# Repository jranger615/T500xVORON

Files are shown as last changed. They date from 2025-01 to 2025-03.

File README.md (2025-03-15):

### If inclined to send a tip for my hard work:
* Paypal: Jeff.b.ranger@gmail.com
* Venmo: @Jeff-Ranger-1

<h2>This is a modificed Voron build using Trist0ne initial configurations but with less complexity. This uses the T500 stock breakout board and will mostly rely on Configuration Changes and Soldering wires/Changing ends for your stealthburner to fit.</h2>

*** 3/5/25 - Update - Changed Printer.cfg, Filament.cfg, and added Runout.cfg. Runout.cfg is commented out in the includes in printer.cfg by default

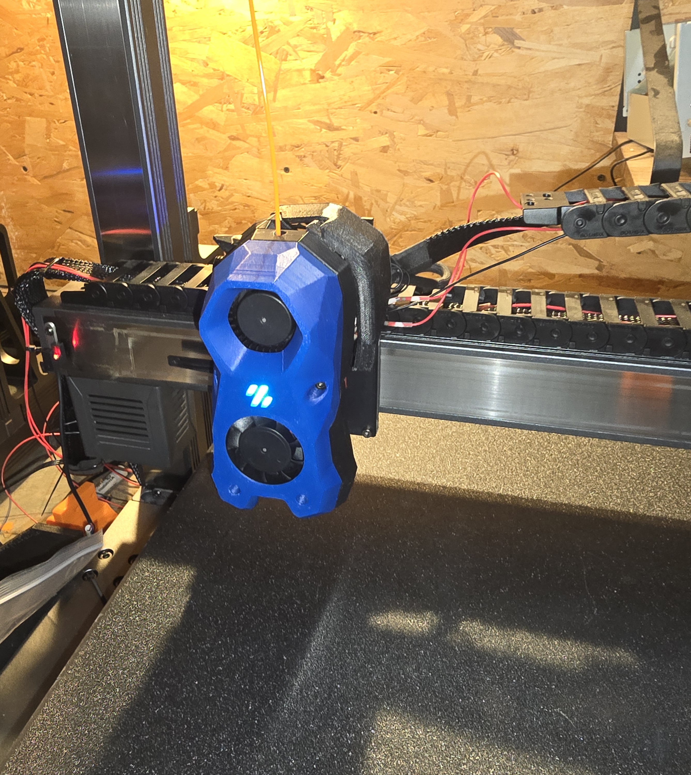
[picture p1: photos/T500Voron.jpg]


## Things to Buy
* If you cant Print ABS or Dont want to print your StealthBurner - [https://www.etsy.com](https://www.etsy.com/search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) and search for Voron StealthBurner. Make sure you get CW2 setup
You will have to talk to the seller and ask him to print all the seperate parts (Board Spacer, Cable Door in STLS, Cable Chain stuff,)

* Optionally you can also use craftcloud.com to have things like the Bed Spacers and T500 Adapter printed in ABS. My Prefered Vendor is 3D Pros 

* BMG Hardened Extruder Parts:
https://west3d.com/products/bmg-components-kit-by-trianglelab?_pos=3&_psq=bm&_ss=e&_v=1.0

* Pancake Motor:
https://west3d.com/products/ldo-nema14-36mm-pancake-stepper-motor-ldo-36sth20-1004ahg

* OPTIONAL Bambu Labs Hotend (Choose HotEnd of Your Choice to replace this) :
https://us.store.bambulab.com/products/bambu-hotend-x1c?variant=40475104313480&currency=USD

* OPTIONAL If Using the Recommended Filament Sensor CW2 you need:
  * [5MM Ball](https://www.amazon.com/dp/B0B5P9H3S2/)
  * [MicroSwitch](https://www.amazon.com/gp/product/B0B3DFJB6P)
 
* OPTIONAL Wiring Pin Conenctors. These can be used instead of cutting your current hot end wires: https://www.amazon.com/1-25mm-Connectors-Pre-Crimped-Pixhawk-Silicone/dp/B07S18D3RN  

* Hardware/FANS/Extruder/Motor Kit: (Use instead of Separate Bolts) (Based on Reviews i dont trust the LEDs or Extruder Parts)
https://a.co/d/hCeWtaP

* 1 Pc RGBW Mini Button PCB LED: (Will need wire extensions to MCU)
https://www.amazon.com/gp/product/B0CDC4SJM8

* LED Connectors for MCU Conenctions https://www.amazon.com/gp/product/B07H1WDN3R/
 
* CHAOTICLAB Voron Tap V2.0:
https://www.amazon.com/dp/B0CJV1QK1N/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

* 3D Printing Soldering Iron
https://www.amazon.com/dp/B0CN6LQXYD/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

* Printing Brass Nuts:
https://www.amazon.com/dp/B09MCWTBCC/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

  * If you use a Bambu Labs hotend, [this](https://www.printables.com/model/588316-stealthburner-bambu-lab-x1cx1-hotend-mount/files) adapter for the StealthBurner works well!
  * A few extra parts you will need:
  * 8x M3 5x4mm heat set inserts (same ones that VORONs use)
  * 8x M4x40mmm Socket Heat Cap Screws (Or whatever style M4x40mm screws you would like, SHCS's are just the easiest to tighten during the build)
  * A small length of PTFE tubing for the Stealthburner hotend mount

## Things to Print
**THESE MUST ALL BE PRINTED FROM ABS OR ASA. THEY ARE DESIGNED FOR ABS. OTHER MATERIALS ARE NOT SUITABLE EITHER DUE TO THEIR TEMPERATURE RESISTANCE OR STRUCTURE CREEP OVER TIME; YOU HAVE BEEN WARNED**
</br>
* FULL OPTIONAL BUILD ZIP(All below components including optional in 1 place) https://github.com/jranger615/T500xVORON/blob/main/FULL_BAMBU_RUNOUT-BUILD-STL.zip
  
  or
  
* [1x Complete Voron Stealthburner Assembly](https://github.com/VoronDesign/Voron-Stealthburner/tree/main)
  * Optionally [but highly reccomended!] use the inline filament runout sensor located [here](https://github.com/jranger615/T500xVORON/blob/main/OptionalSTLS/CW2_main_fil_sen_2023.stl). This replaces the main_body of the CW2 extruder.
  * Optionally Bambu Labs hotend, [this](https://github.com/jranger615/T500xVORON/tree/main/OptionalSTLS) adapter for the StealthBurner works well!
  * Ensure you use the [Custom Cable_Cover](https://github.com/jranger615/T500xVORON/blob/main/STL/cable_door_for_T500.stl)
  * [Toolhead T500 spacer](https://github.com/jranger615/T500xVORON/blob/main/STL/T500-Board-Adapter.stl.stl)(Requires 1 heat insert)
   * You do not need to print the gantry mount or TAP mount; the extruder and toolhead cover screw directly into the CNC TAP
* [T500 TAP Adapter](https://github.com/jranger615/T500xVORON/blob/main/STL/T500%20TAP%20Adapter.stl)
* [2x Bed Spacers](https://github.com/jranger615/T500xVORON/blob/main/STL/Bed%20Spacer%20T500%20v3.stl). Ensure these print perfectly flat with no warping, or it will throw off your bed level!
* Optional for Cable Management/Ribbon Cable Retainer [3 Hole Cable Bridge](https://github.com/VoronDesign/Voron-Stealthburner/blob/main/STLs/Clockwork2/chain_anchor_3hole_SW.stl) & [Retainer](https://github.com/jranger615/T500xVORON/blob/main/STL/T500%20Ribbon%20Cable%20Retainer%20%26%20Cable%20Connector.stl) (Retainer requires 2 heat inserts to attach cable chain)

Print Settings:
* Layer height: 0.2mm
* Extrusion width: 0.4mm, forced
* Infill percentage: 40%
* Infill type: grid, gyroid, honeycomb, triangle, or cubic
* Wall count: 4
* Solid top/bottom layers: 5
* Supports: NONE

## The Build
You can do the following sections in any order, they are just listed in the order I did them. **Some of the steps will be linked to other guides** for the non-T500 conversion specific parts as they cover them more in depth, and there's no need to reinvent the wheel.

### Prerequisites
* Assemble the VORON Stealthburner
  * Follow the build guide located [here](https://github.com/VoronDesign/Voron-Stealthburner/tree/main/Manual). This is a large step, and your toolhead will only function as well as you assemble it, so take your time.
  * this video is also helpful https://youtu.be/dOyYvnehLaI?si=HIRMF422sOZMZnhB

### Mounting the Toolhead
1. Start by inserting {4x} M3 5x4mm heat set inserts into the adapter plate. Take care to ensure they are perfectly level with the surface of the plastic.
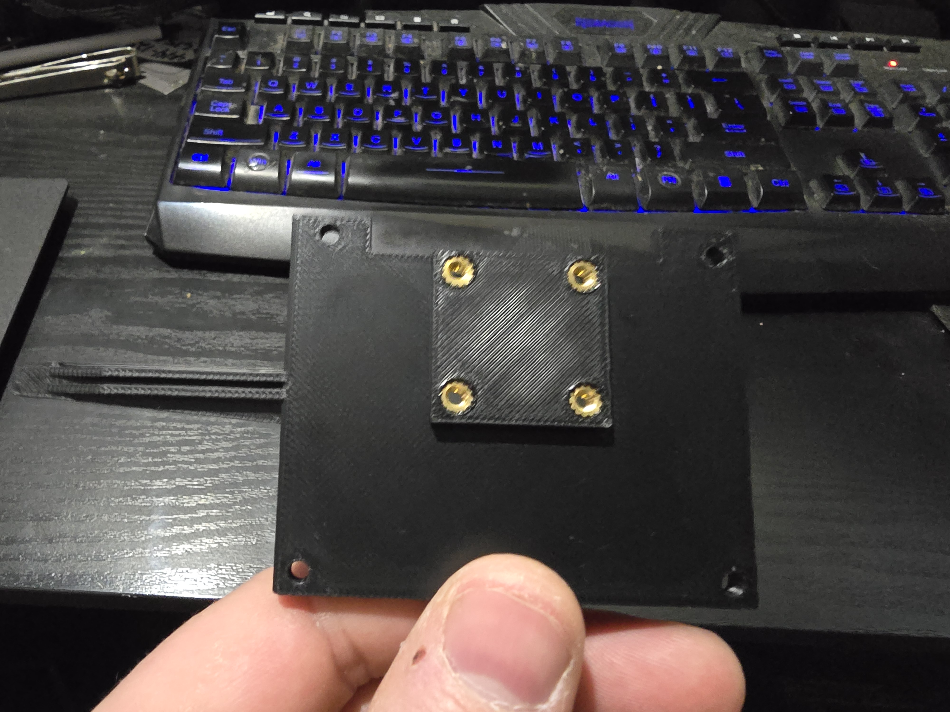
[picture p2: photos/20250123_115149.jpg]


2. Unclip the stock toolhead umbilical and drag chain mount, and move them out of the way. Unmount the stock T500 toolhead and drag chain plate. There are 4 screws around the outside of the plastic casing (keep these!), several screws holding the drag chain plate to the rail. You should be left with a metal rectangular sliding rail.
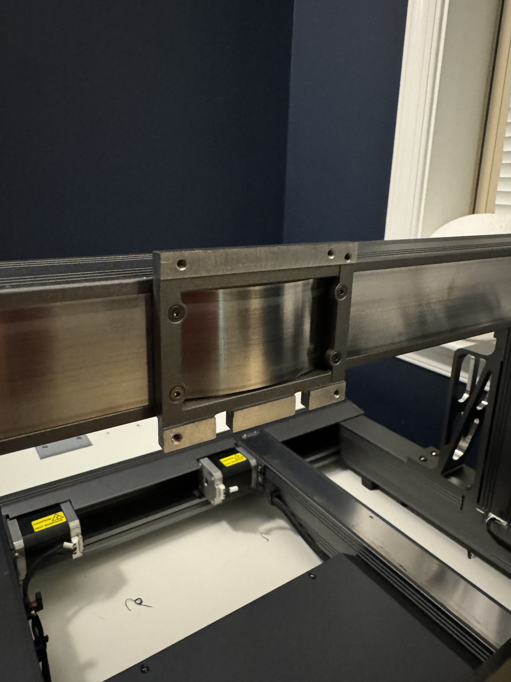
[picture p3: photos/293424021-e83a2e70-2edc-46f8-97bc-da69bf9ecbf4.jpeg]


3. Using the 4 casing screws from the stock toolhead, attach the Adapter Plate to the rectangular sliding rail. Check to ensure the rail still slides back and forth. 
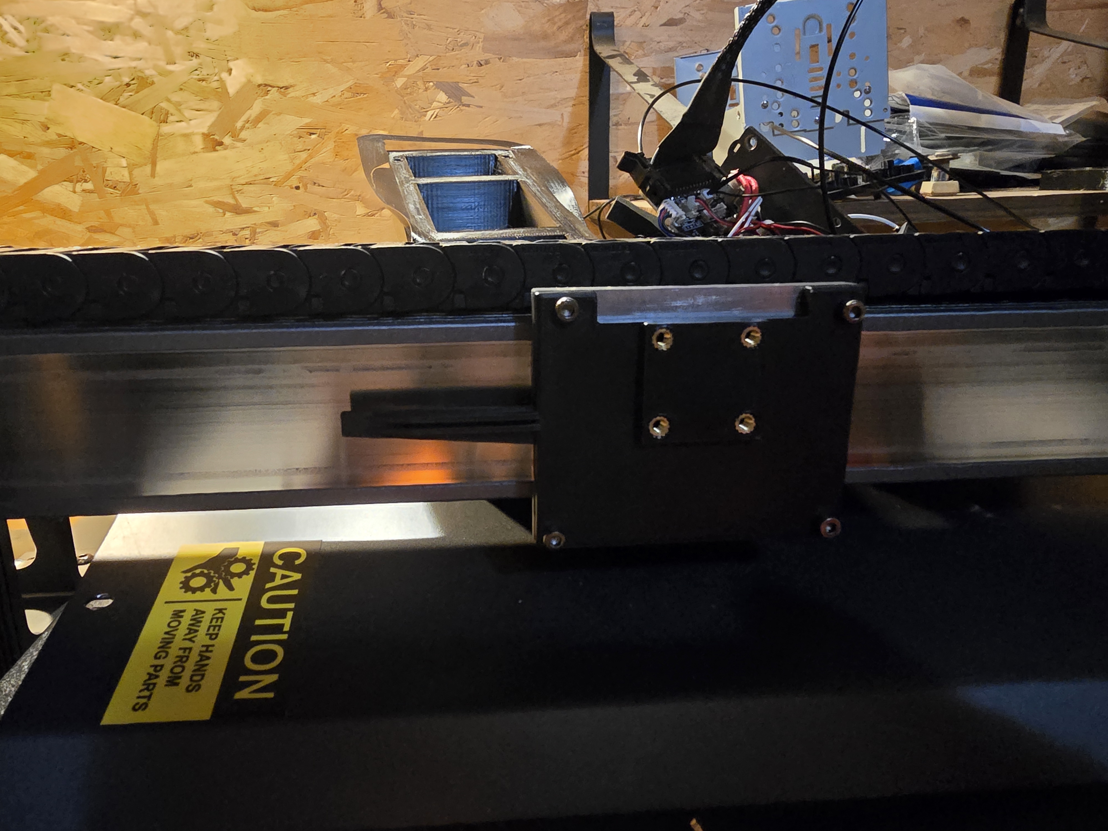
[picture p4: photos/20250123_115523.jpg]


4. Attach the ChaoticLabs CNC TAP to the Adapter Plate
   * The attachment process is the same as the one located in the [CNC TAP build guide](https://github.com/Chaoticlab/CNC-Tap-for-Voron/blob/master/Manual/CNC_Voron_Tap_Build_Guide.pdf)
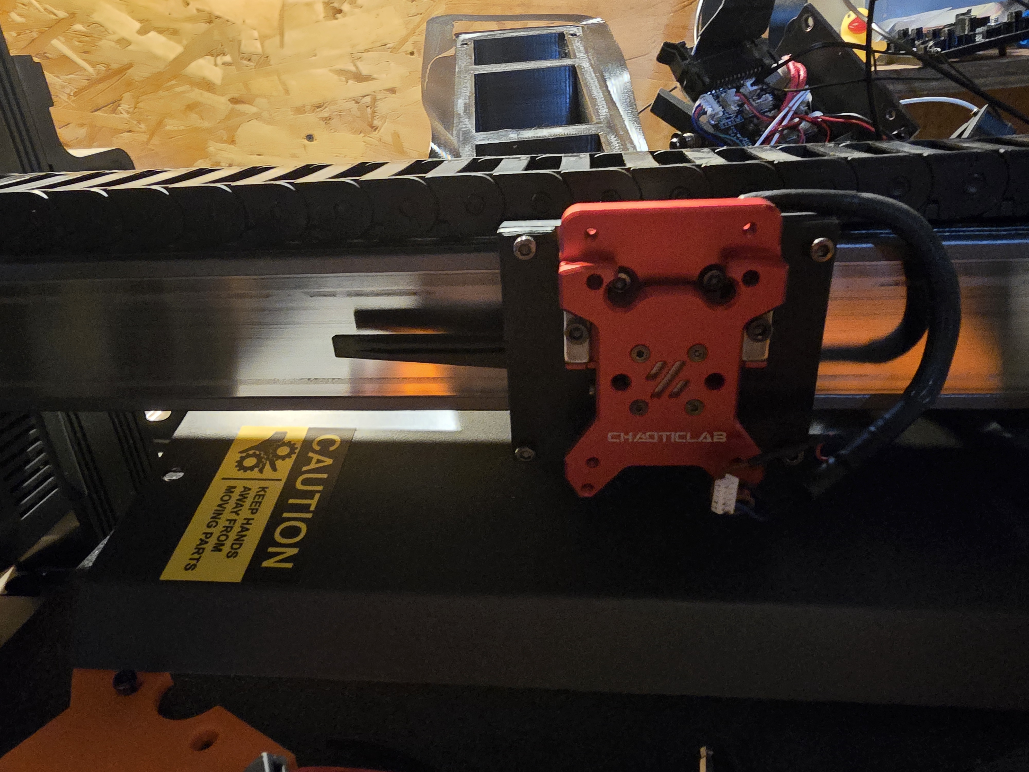
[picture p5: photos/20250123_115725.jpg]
   * 

5. Attach the Stealthburner assembly to the CNC TAP. Check to make sure the whole assembly can slide up and down (the 'TAP' function)
   * The attachment process for the Stealthburner is the same as the one located in the [CNC TAP build guide](https://github.com/Chaoticlab/CNC-Tap-for-Voron/blob/master/Manual/CNC_Voron_Tap_V2_Build_Guide_20231013.pdf)
 
6. Check clearences, and appreciate how nice the Stealthburner looks mounted on the T500

#### X Endstop Move
**IF YOU DONT DO THIS, YOUR X Will not have an endstop setup and will crash**
 * The X End Stop is on the back of the X Axis. Remove the Screw and move it to the lower front bolt that holds the X Axis cover. (THis will requie a slightly logner m3 bolt)
 * Using washers, Center the X End Stop with the new Carriage assembly.
 * WIth the Machine Powered on, you should see the red light Turn off as the plastic extension passes into it.
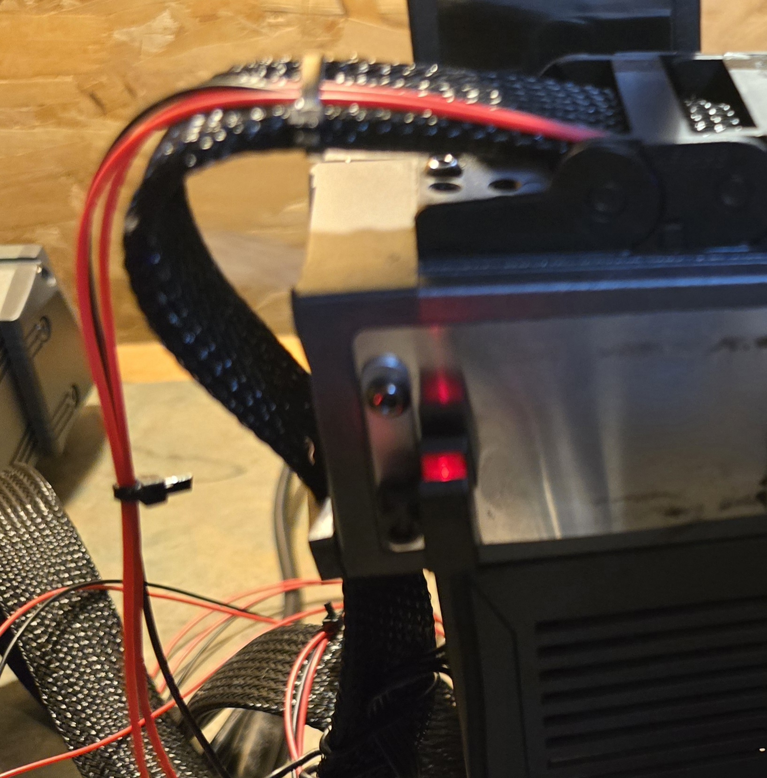
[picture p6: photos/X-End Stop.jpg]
 *

### Raising the Bed
The stock T500 gantry and bed are mounted in such a way that the gantry cannot drop low enough to touch the nozzle to the bed. Obviously, this is problematic. Because of the way the gantry is designed, there is no easy way to gracefully drop the toolhead low enough; thus, we have to go the other direction and raise the bed!
* "Wont I lose Z height??"
  * Nope! In it's stock form, the T500 Z rails can raise the nozzle up to 550mm. With these spacers in place, you will still have 520mm of Z clearance (though it will still be software limited to 500mm), so there is no lost Z build height!
* "Wont these spacers melt so close to the bed? Are they strong enough?"
  * Nope! They're far enough from the bed that they are well within the longterm operating temperature limit of ABS. ABS also does not stress creep over time, and should remain durable for the life of the printer
 
1. Remove the print surface, and remove the 8x M4 socket head screws using the access holes
   * 

   * If you have a difficult time getting a tool to fit in those holes, you can unbolt every M4 countersunk screw and remove the headbed entirely.
   * If you remove the bed from the bed frame, remove the screws holding the bed drag chain to the bed frame
   * 

2. Carefully raise the bed frame, and align the bed spacers to the long rectangular rails
   * Be very careful not to damage the heatbed wiring!


   * Depending on how much your ABS print shrunk, you may need to slightly drill out the holes in the printed bed spacers; you'll never get them properly aligned unless the screws can slide through the spacers with only light resistance


3. Using 8x M4x40mm screws, bolt the bed frame to the Y axis rails through the spacers. Ensure everything is very tight and does not have any play; you dont want your bed level changing or your bed flying off its rails!


4. If you removed it in step 1, reattach the drag chain to the bed frame

5. Check to ensure the bed is able to slide **all** the way back and forth across its rails. If you did not use M4x40mm screws to attach the spacers, they may stick out from the rails and hit the Y Stepper drivers.

### Mounting PCB
* Mount your PCB Spacer using a m3x8 to the inner most heat insert. You may want to use a m3 bolt at the top to hold it in palce before you tighten it down.
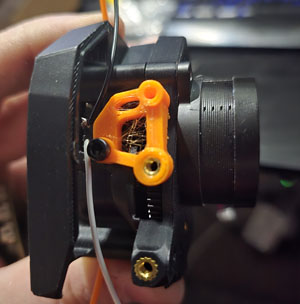
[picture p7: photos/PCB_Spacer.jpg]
  * 
* Use a small m3 bolt to mount the board to the spacer. Make sure its not too long or it may hit the gear
* Use a m3x10 (May be 12) to mount the top location of the board
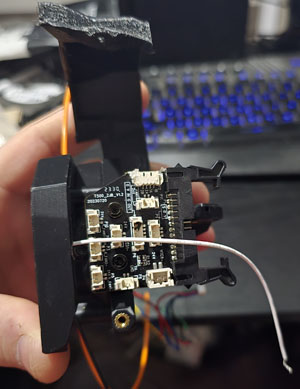
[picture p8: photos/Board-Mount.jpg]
  * 

### Wiring Wiring Wiring
Printer should be **fully powered off and unplugged** for the next few steps.
* I cut and soldered all connectors from the original hotend. I believe these are MINI JST Connectors but i am unsure so i just used what i had.

# Stock Breakout Board Connections
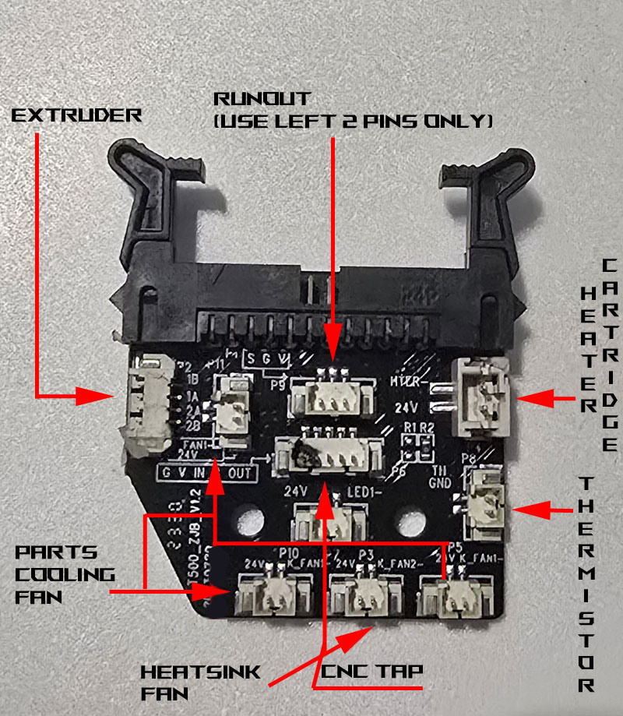
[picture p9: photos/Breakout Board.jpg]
* 

# Motor Wiring
 * Cut your Stock Wiring Harness and the LDO Wiring Harness from each Motor
 * Match LDO Wires to Stock Wire Harness Below
   * A2 Blue > Blue 1B
   * A1 Yellow > RED 1A
   * B1 Green > Green 2B
   * B2 Red > Black 2B
     
# TAP Wiring
For Reference ONLY: Pull Up Indicator and Reverse Polarity indicator were needed for the TAP ^!PE8

 * Cut your Sensor Wire off the TAP and Off the Thermal Sensor
 * Match TAP Wires to Stock Wiring
   * Red Wire > Brown Wire
   * Black Wire > Blue Wire
   * Yellow Wire > Black Wire 

 # RunOut Sensor
 For Reference ONLY: Reverse Polarity was needed for this function !PE9
 
 * The Runout sensor will only use 2 connections
   * Outside Connections(Button Side) To the Left Most Pin on the Breakout Board
   * Middle Connections to Ground or Middle Pin on the Breakout Board
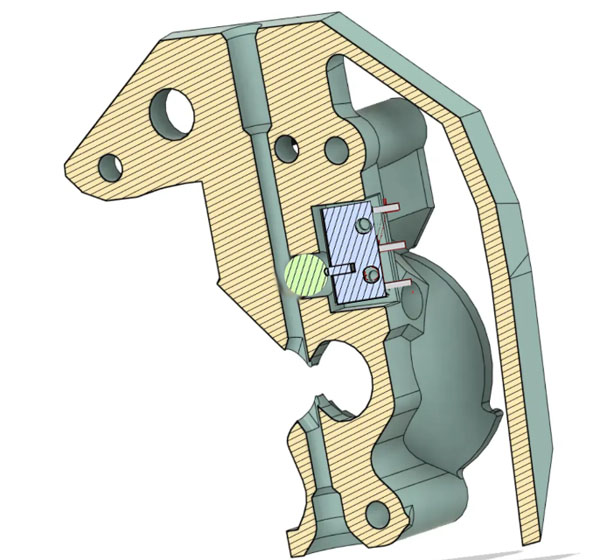
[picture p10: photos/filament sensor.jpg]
 
 
 # FANS
 * Red/Black wires will all match for 24v Fans
 * Heatsink Fan is the middle Fan connector on the bottom 3
 * Cooling Fan can attach to any of the other 3 connectors

 # HotEnd
  * These wires you cant really wire wrong as long as you plug the right connection in.
  * The thermistor is usually the bare copper looking wire comming off the Hot End
  * Heat Cartidge is usually a thicker set of wires with insulation

# LED Wiring
 * You will need to access the mother board and run a long set of 3 wires to the mainboard.
 * Feed all the wires through the cable chain and amtch them to the length of the ribbon cable. I zipped tied them along it after exiting the cable chain,
 * See the below diagram to connect the wires
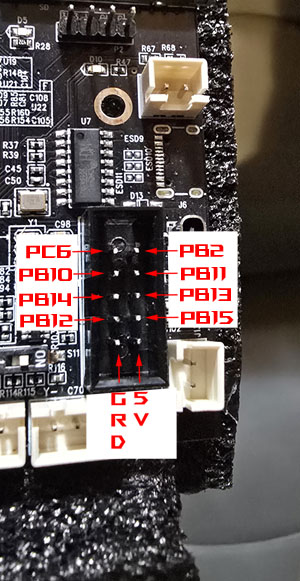
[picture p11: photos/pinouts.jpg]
   * 
   * Connect the Middle DataWire to PB12 (Usually Blue),
   * Connect the 2 outside connections to the 2 bottom pins 5v and Ground as it shows on the LEDS.
  
# Ribbon Cable/Retainer
  * Attach the ribbon Cable to the breakout board
  * If you printed the retainer you can now install it to keep the ribbon cable from pulling free
  * Attach Cable Chain to Retainer. 

### Software Configuration

#### Initial Startup
1. SSH into your printer. The username is **mks**, and the password is **makerbase**. Install KAMP on your printer, located [here](https://github.com/kyleisah/Klipper-Adaptive-Meshing-Purging)
2. Access your printers web-ui. In the machine tab, delete ALL the follwing if present: filament.cfg, KAMP_Settings.cfg,macros.cfg, mainsail.cfg,moonraker.conf,printer.cfg,start.cfg,stealthburner_leds.cfg,temperature_led.cfg,runout.cfg and toolhead.cfg
3. Download the Klipper Configurations folder from this Github ([here](https://github.com/jranger615/T500xVORON/tree/main/configs)), and upload them ALL to the printer's config section.
* 
4. RUnout.cfg is commented out in printer.cfg by default. If you are using a runout sensor un-comment this at the top of printer.cfg 
5. Configure the annotated sections of **toolboard.cfg**. Things like Nozzle Size, PID Tunning, Extruder Sensor Typer, and Rotation Distance need to be adjusted for your machine.
6. Save and click 'firmware restart'; resolve any errors that Klipper may throw, if any (the error message will tell you what the configuration issue is).

#### Z Offset Configuration
Update your Z offset
* Remember, with Tap, your nozzle IS the probe. You'll need to manually calibrate the probe's Z offset by using PROBE_CALIBRATE and your chosen leveling method (I use a sheet of paper)

### Final Checks
1. Ensure that your printer can reliably home X, Y, and Z.
2. Test that your Extruder, Hotend, Hotend Fan, Part Cooling Fan, and [optionally] the runout sensor all work as expected.
3. PID Calibrate your Hotend following [this guide](https://www.obico.io/blog/klipper-pid-tuning/)
4. Follow the [Ellis3dp print tuning guide](https://ellis3dp.com/Print-Tuning-Guide/articles/extruder_calibration.html) to dial in your Stealthburner
5. Configure Input Shaping on both X and Y
* You can reference [this guide](https://www.klipper3d.org/Measuring_Resonances.html#bed-slinger-printers) for help
* I use the SHAPER_CALIBRATE macro for automatic calibration. It will measure both X and Y sequentially and apply the best settings automatically. 

6. Retune your Pressure Advance
* Follow [this guide](https://github.com/SoftFever/OrcaSlicer/wiki/Calibration) from the Orca Slicer wiki. You shold set this number in the Orca Slicer filament profile settings, rather than setting it in the Klipper configs. It will be different for every filament and between brands. 
7. Pat yourself on the back for a job well done! Edit your slicer settings as shown below, and then do a test print!

### Slicer Configuration
1. Edit your printer settings "Machine G-code" tab as follows:
* PRINT_START EXTRUDER=[nozzle_temperature_initial_layer] BED=[bed_temperature_initial_layer_single] CHAMBER=[chamber_temperature]
* PRINT_END
* 
3. In the 'Others' tab, enable
* Label Objects
* Exclude Objects

### Troubleshooting Notes
There are two errors you may see in your console when starting a print:
1. Unknown command:"SAVE_LAST_FILE"
2. Error evaluating 'gcode_macro PRINT_START:gcode': jinja2.exceptions.UndefinedError: 'dict object' has no attribute 'BED'
These are caused by the non-standard version of klipperscreen that comes built into the T500, and makes calls to incorrectly labeled markers. **Thankfully, they don't actually impede the printing, so you can ignore them!** You can resolve this by installing the standard version of KlipperScreen using [KIAUH](https://github.com/dw-0/kiauh), which comes built into the T500

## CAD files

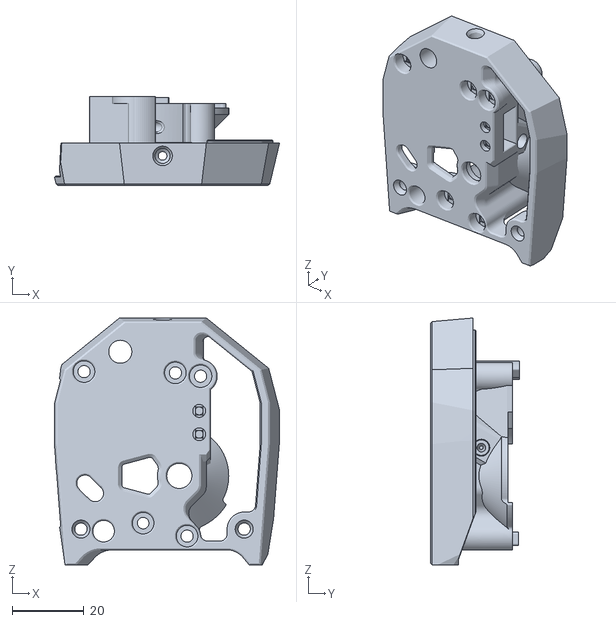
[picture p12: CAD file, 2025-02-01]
OptionalSTLS/CW2_main_fil_sen_2023.stl
62.6 x 24.7 x 68.7

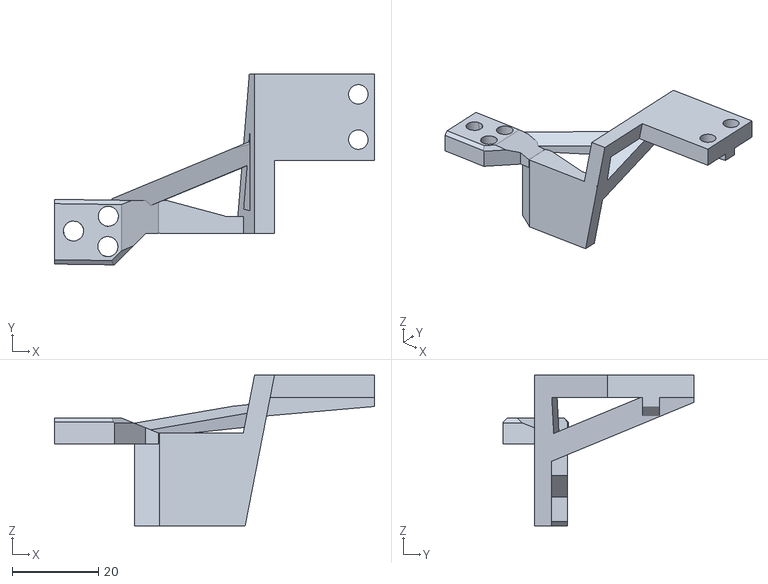
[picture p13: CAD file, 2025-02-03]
STL/T500 Ribbon Cable Retainer & Cable Connector.stl
74.2 x 44.2 x 35.0

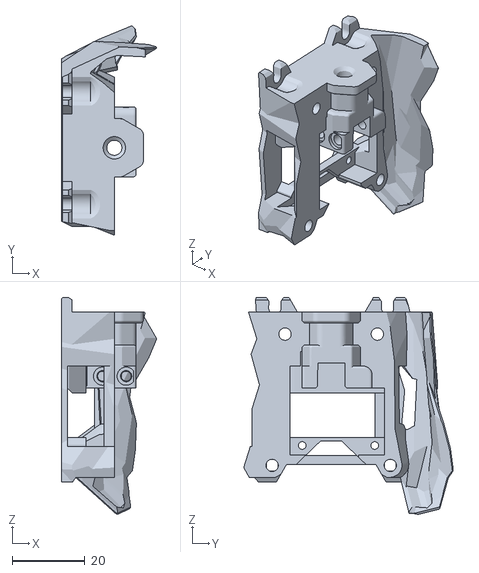
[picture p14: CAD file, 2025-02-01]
OptionalSTLS/SB_Bambu_ Back.stl
26.3 x 57.7 x 59.7

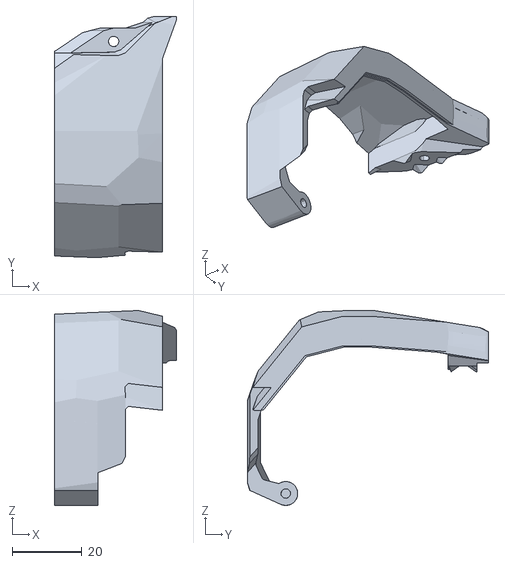
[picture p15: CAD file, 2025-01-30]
STL/cable_door_for_T500.stl
35.2 x 69.4 x 56.1

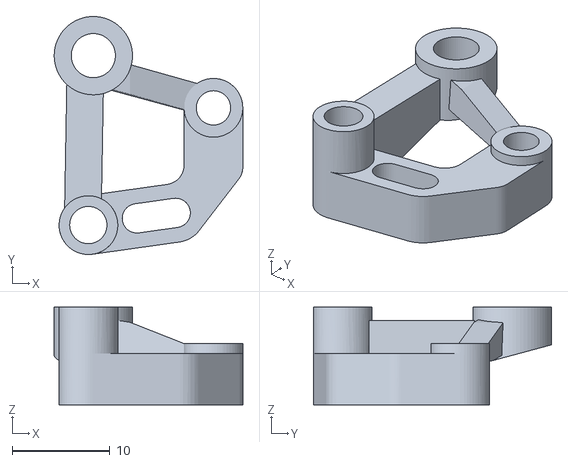
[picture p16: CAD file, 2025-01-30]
STL/T500-Board-Adapter.stl.stl
19.3 x 24.3 x 10.0

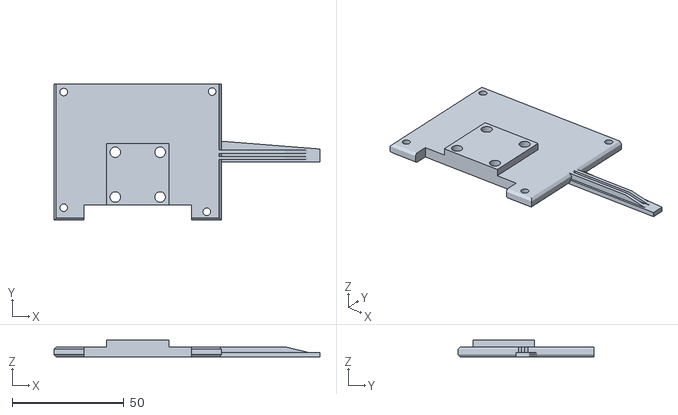
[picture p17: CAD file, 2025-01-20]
STL/T500 TAP Adapter.stl
118.8 x 60.8 x 7.50

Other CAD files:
OptionalSTLS/SB_Bambu_Front.stl

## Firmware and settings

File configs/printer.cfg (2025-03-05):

## CREATED BY @Trist0ne

########################################################################################################################### CONFIG INCLUDES
[include KAMP_Settings.cfg]
[include stealthburner_leds.cfg]
[include temperature_led.cfg]
[include toolhead.cfg]
[include start.cfg]
[include filament.cfg]
[include macros.cfg]
#[include runout.cfg]
########################################################################################################################### MCU

[mcu]
serial:/dev/serial/by-id/usb-1a86_USB_Serial-if00-port0
restart_method: command

[mcu rpi]
serial: /tmp/klipper_host_mcu

########################################################################################################################### SPEED/ACCEL SETTINGS

[printer]
kinematics: cartesian
max_velocity: 300
max_accel: 3000
max_accel_to_decel: 1500
max_z_velocity: 15
max_z_accel: 100
square_corner_velocity:2

########################################################################################################################### MAINSAIL MISC

[virtual_sdcard]
path: ~/printer_data/gcodes
on_error_gcode: CANCEL_PRINT

[pause_resume]

[exclude_object]

[display_status]

[gcode_arcs]
resolution: 0.1

[idle_timeout]
timeout: 3600
#   Idle time (in seconds) to wait before running the above G-Code
#   commands. The default is 600 seconds.

########################################################################################################################### INPUT SHAPER
[delayed_gcode set_temeperature_leds]
initial_duration: 1
gcode:
     STATUS_READY


[adxl345]
cs_pin: rpi:None
spi_bus: spidev0.0

[input_shaper]
damping_ratio_x: 0.05
damping_ratio_y: 0.1
shaper_type_x = 3hump_ei
shaper_freq_x = 52.4
shaper_type_y = 2hump_ei
shaper_freq_y = 25

[resonance_tester]
accel_chip: adxl345
probe_points:230, 230, 20  # an example
accel_per_hz:50
min_freq:1
max_freq:100
max_smoothing:0.2
hz_per_sec:0.5

########################################################################################################################### HEATER CHECKS

[verify_heater extruder]
max_error: 60
check_gain_time:20
hysteresis: 5
heating_gain: 2

[verify_heater heater_bed]
max_error: 240
check_gain_time:180
hysteresis: 5
heating_gain: 1 

########################################################################################################################### STEPPER X

[stepper_x]
step_pin: PE2
dir_pin: PE0
enable_pin: !PE3
microsteps: 16
rotation_distance: 72
endstop_pin: ^PE15
position_endstop: -5
position_min: -5
position_max: 505
homing_speed: 80
step_pulse_duration:0.000002

[tmc2209 stepper_x]
uart_pin: PE1
run_current: 1.5
uart_address: 3
#stealthchop_threshold: 999999
driver_TBL: 2
driver_TOFF: 2
driver_HEND: 1
driver_HSTRT: 4
driver_PWM_LIM: 8 
driver_PWM_GRAD: 8
driver_PWM_FREQ: 1
driver_PWM_REG: 4

########################################################################################################################### STEPPER Y

[stepper_y]
step_pin: PB8
dir_pin: !PB6
enable_pin: !PB9
microsteps: 16
rotation_distance: 72
endstop_pin: ^PE13 
position_endstop: -30
position_min: -30
position_max: 503
homing_speed: 80
step_pulse_duration:0.000002


[tmc2209 stepper_y]
uart_pin: PB7
run_current: 1.5
uart_address: 3
#stealthchop_threshold: 999999

[stepper_y1]
step_pin:PD7
dir_pin:PD0
enable_pin:!PB5
microsteps:16
rotation_distance:72
endstop_pin: ^PE13

[tmc2209 stepper_y1]
uart_pin:PD1
run_current:1.5 
uart_address:3
#stealthchop_threshold: 999999

########################################################################################################################### STEPPER Z

[stepper_z]
step_pin: PD15
dir_pin: !PD13
enable_pin: !PA12
microsteps: 16
rotation_distance: 4
endstop_pin:probe:z_virtual_endstop
position_max: 505
position_min: -3
homing_speed: 10

[tmc2209 stepper_z]
uart_pin:PD14
run_current:0.6
uart_address:3
stealthchop_threshold: 999999

[stepper_z1]
step_pin: PD11
dir_pin: !PD9
enable_pin: !PD12
microsteps: 16
rotation_distance: 4
endstop_pin:probe:z_virtual_endstop

[tmc2209 stepper_z1]
uart_pin:PD10
run_current:0.6
uart_address:3
stealthchop_threshold: 999999

########################################################################################################################### PROBE

[probe]
pin:^!PE8
x_offset: 0
y_offset: 0
#z_offset: -1.42
speed: 10.0
samples: 3
samples_result: median
sample_retract_dist: 3.0
samples_tolerance: 0.006
samples_tolerance_retries: 10
activate_gcode:
    {% set PROBE_TEMP = 275 %}
    {% set MAX_TEMP = PROBE_TEMP + 5 %}
    {% set ACTUAL_TEMP = printer.extruder.temperature %}
    {% set TARGET_TEMP = printer.extruder.target %}

    {% if TARGET_TEMP > PROBE_TEMP %}
        { action_respond_info('Extruder temperature target of %.1fC is too high, lowering to %.1fC' % (TARGET_TEMP, PROBE_TEMP)) }
        M109 S{ PROBE_TEMP }
    {% else %}
        # Temperature target is already low enough, but nozzle may still be too hot.
        {% if ACTUAL_TEMP > MAX_TEMP %}
            { action_respond_info('Extruder temperature %.1fC is still too high, waiting until below %.1fC' % (ACTUAL_TEMP, MAX_TEMP)) }
            TEMPERATURE_WAIT SENSOR=extruder MAXIMUM={ MAX_TEMP }
        {% endif %}
    {% endif %}




########################################################################################################################### Z HOMING

[safe_z_home]
home_xy_position: 250,250
speed: 90
z_hop: 5                 # Move up 5mm
z_hop_speed: 5

########################################################################################################################### BED MESH

[bed_mesh]
speed:190                
horizontal_move_z:3   
mesh_min:26,26   
mesh_max:478,474 
probe_count:10,10    
mesh_pps: 2, 3
algorithm: bicubic
bicubic_tension: 0.2 



########################################################################################################################### Z TILT

[z_tilt]
z_positions: 97, 250
             409, 250
points: 97, 250
        409, 250
speed: 200
horizontal_move_z: 5
retries: 20
retry_tolerance: .005

########################################################################################################################### FANS
[fan]
pin: PA1

[controller_fan Fan_Board]
pin:PA3
fan_speed: 1.0
idle_timeout: 120
heater: heater_bed, extruder
stepper: stepper_x, stepper_y, stepper_y1, stepper_z, stepper_z1


	

########################################################################################################################### AUTO GENERATED

#*# <---------------------- SAVE_CONFIG ---------------------->
#*# DO NOT EDIT THIS BLOCK OR BELOW. The contents are auto-generated.
#*#
#*# [probe]
#*# z_offset = -0.470
#*#
#*# [extruder]
#*#
#*# [bed_mesh default]
#*# version = 1
#*# points =
#*# 	  -0.053750, -0.065000, -0.017500
#*# 	  -0.060000, -0.086250, -0.083750
#*# 	  -0.083750, -0.113750, -0.126250
#*# x_count = 3
#*# y_count = 3
#*# mesh_x_pps = 2
#*# mesh_y_pps = 3
#*# algo = lagrange
#*# tension = 0.2
#*# min_x = 221.79
#*# max_x = 279.43
#*# min_y = 227.61
#*# max_y = 281.59
#*#
#*# [input_shaper]

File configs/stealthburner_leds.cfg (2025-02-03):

# Macros for setting the status leds on the Voron StealthBurner toolhead (or for any neopixel-type leds).
#
# You will need to configure a neopixel (or other addressable led, such as dotstar). See
# https://www.klipper3d.org/Config_Reference.html#neopixel for configuration details.


#####################################
#           INSTRUCTIONS            #
#####################################
# How to use all this stuff:
#
#     1.  Copy this .cfg file into your Klipper config directory and then add [include stealthburner_leds.cfg]
#         to the top of your printer.cfg in order to register the LEDs and macros with Klipper.
#     2.  Define your LEDs by editing [neopixel sb_leds] below and entering the data pin from your control board
#         as well as the color order.
#
#           Note: RGB and RGBW are different and must be defined explicitly.  RGB and RGBW are also not able to 
#                 be mix-and-matched in the same chain. A separate data line would be needed for proper functioning.
#
#                 RGBW LEDs will have a visible yellow-ish phosphor section to the chip.  If your LEDs do not have
#                 this yellow portion, you have RGB LEDs.
#
#     3.  Save your config and restart Klipper.
#
#           Note: We set RED and BLUE to 1.0 to make it easier for users and supporters to detect 
#                 misconfigurations or miswiring. The default color format is for Neopixels with a dedicated 
#                 white LED. On startup, all three SB LEDs should light up.
#
#                 If you get random colors across your LEDs, change the color_order to GRB and restart. Then
#                 omit the W for each suggested color_order in the next paragraph.
#
#                 If you get MAGENTA, your  color order is correct. If you get CYAN, you need to use RGBW. If
#                 you get YELLOW, you need to use BRGW (note that BRG is only supported in the latest Klipper
#                 version).
#
#     4.  Once you have confirmed that the LEDs are set up correctly, you must now decide where you want 
#         these macros called up...which means adding them to your existing gcode macros.  NOTHING will happen
#         unless you add the STATUS_????? macros to your existing gcode macros.  
#
#           Example: add STATUS_LEVELING to the beginning of your QGL gcode macro, and then add STATUS_READY 
#                    to the end of it to set the logo LED and nozzle LEDs back to the `ready` state.
#
#           Example: add STATUS_CLEANING to the beginning of your nozzle-cleaning macro, and then STATUS_READY
#                    to the end of it to return the LEDs back to `ready` state.
#
#     5.  Feel free to change colors of each macro, create new ones if you have a need to.  The macros provided below
#         are just an example of what is possible.  If you want to try some more complex animations, you will most
#         likely have to use WLED with Moonraker and a small micro-controller 
#
#####################################
#       END INSTRUCTRUCTIONS        #
#####################################


[neopixel sb_leds]
pin: PB12#   The pin connected to the neopixel. This parameter must be provided.
chain_count: 3
#   The number of Neopixel chips that are "daisy chained" to the
#   provided pin. The default is 1 (which indicates only a single
#   Neopixel is connected to the pin).
color_order: GRBW
#   Set the pixel order required by the LED hardware. Options are GRB,
#   RGB, GRBW, or RGBW. The default is GRB.
initial_RED: 0.0
initial_GREEN: 0.0
initial_BLUE: 0.0
initial_WHITE: 1.0
#   Sets the initial LED color of the Neopixel. Each value should be
#   between 0.0 and 1.0. The WHITE option is only available on RGBW
#   LEDs. The default for each color is 0.#

# Most configuration for the macros can be done by modifying the variables in the _sb_vars macro
# at the start of this file.

##########
# MACROS #
##########

# The following status macros are available (these go inside of your macros):
#
#    STATUS_READY
#    STATUS_OFF
#    STATUS_BUSY
#    STATUS_HEATING
#    STATUS_LEVELING
#    STATUS_HOMING
#    STATUS_CLEANING
#    STATUS_MESHING
#    STATUS_CALIBRATING_Z
#
# With additional macros for basic control:
#
#    SET_NOZZLE_LEDS_ON
#    SET_LOGO_LEDS_OFF
#    SET_NOZZLE_LEDS_OFF
#
# Contributed by Voron discord users wile.e, Tetsunosuke, and etherwalker


[gcode_macro _sb_vars]
# User settings for the StealthBurner status leds. You can change the status colors and led
# configurations for the logo and nozzle here.
variable_colors: {
        'logo': { # Colors for logo states
            'busy': {'r': 0.4, 'g': 0.0, 'b': 0.0, 'w': 0.0},
            'cleaning': {'r': 0.0, 'g': 0.02, 'b': 0.5, 'w': 0.0},
            'calibrating_z': {'r': 0.8, 'g': 0., 'b': 0.35, 'w': 0.0},
            'heating': {'r': 0.3, 'g': 0.18, 'b': 0.0, 'w': 0.0},
            'homing': {'r': 0.0, 'g': 0.6, 'b': 0.2, 'w': 0.0},
            'leveling': {'r': 0.5, 'g': 0.1, 'b': 0.4, 'w': 0.0},
            'meshing': {'r': 0.2, 'g': 1.0, 'b': 0.0, 'w': 0.0},
            'off': {'r': 0.0, 'g': 0.0, 'b': 0.0, 'w': 0.0},
            'printing': {'r': 1.0, 'g': 0.0, 'b': 0.0, 'w': 0.0},
            'standby': {'r': 0.00, 'g': 0.5, 'b': 0.5, 'w': 0.0},
        },
        'nozzle': { # Colors for nozzle states
            'heating': {'r': 0.8, 'g': 0.35, 'b': 0.0, 'w':0.0},
            'off': {'r': 0.0, 'g': 0.0, 'b': 0.0, 'w': 0.0},
            'on': {'r': 0.8, 'g': 0.8, 'b': 0.8, 'w':1.0},
            'standby': {'r': 0.0, 'g': 0.0, 'b': 0.0, 'w':0.0},
        },
        'thermal': {
            'hot': {'r': 1.0, 'g': 0.0, 'b': 0.0, 'w': 0.0},
            'cold': {'r': 0.3, 'g': 0.0, 'b': 0.3, 'w': 0.0}
        }
    }
variable_logo_led_name:         "sb_leds" 
# The name of the addressable LED chain that contains the logo LED(s)
variable_logo_idx:              "1" 
# A comma-separated list of indexes LEDs in the logo
variable_nozzle_led_name:       "sb_leds"
# The name of the addressable LED chain that contains the nozzle LED(s). This will
# typically be the same LED chain as the logo.
variable_nozzle_idx:            "2,3"
# A comma-separated list of indexes of LEDs in the nozzle
gcode:
    # This section is required.  Do Not Delete.


[gcode_macro _set_sb_leds]
gcode:
    {% set red = params.RED|default(0)|float %}
    {% set green = params.GREEN|default(0)|float %}
    {% set blue = params.BLUE|default(0)|float %}
    {% set white = params.WHITE|default(0)|float %}
    {% set led = params.LED|string %}
    {% set idx = (params.IDX|string).split(',') %}
    {% set transmit_last = params.TRANSMIT|default(1) %}

    {% for led_index in idx %}
        {% set transmit=transmit_last if loop.last else 0 %}
        set_led led={led} red={red} green={green} blue={blue} white={white} index={led_index} transmit={transmit}
    {% endfor %}

[gcode_macro _set_sb_leds_by_name]
gcode:
    {% set leds_name = params.LEDS %}
    {% set color_name = params.COLOR %}
    {% set color = printer["gcode_macro _sb_vars"].colors[leds_name][color_name] %}
    {% set led = printer["gcode_macro _sb_vars"][leds_name + "_led_name"] %}
    {% set idx = printer["gcode_macro _sb_vars"][leds_name + "_idx"] %}
    {% set transmit = params.TRANSMIT|default(1) %}

    _set_sb_leds led={led} red={color.r} green={color.g} blue={color.b} white={color.w} idx="{idx}" transmit={transmit}

[gcode_macro _set_logo_leds]
gcode:
    {% set red = params.RED|default(0)|float %}
    {% set green = params.GREEN|default(0)|float %}
    {% set blue = params.BLUE|default(0)|float %}
    {% set white = params.WHITE|default(0)|float %}
    {% set led = printer["gcode_macro _sb_vars"].logo_led_name %}
    {% set idx = printer["gcode_macro _sb_vars"].logo_idx %}
    {% set transmit=params.TRANSMIT|default(1) %}

    _set_sb_leds led={led} red={red} green={green} blue={blue} white={white} idx="{idx}" transmit={transmit}

[gcode_macro _set_nozzle_leds]
gcode:
    {% set red = params.RED|default(0)|float %}
    {% set green = params.GREEN|default(0)|float %}
    {% set blue = params.BLUE|default(0)|float %}
    {% set white = params.WHITE|default(0)|float %}
    {% set led = printer["gcode_macro _sb_vars"].nozzle_led_name %}
    {% set idx = printer["gcode_macro _sb_vars"].nozzle_idx %}
    {% set transmit=params.TRANSMIT|default(1) %}

    _set_sb_leds led={led} red={red} green={green} blue={blue} white={white} idx="{idx}" transmit={transmit}

[gcode_macro set_logo_leds_off]
gcode:
    {% set transmit=params.TRANSMIT|default(1) %}
    _set_logo_leds red=0 blue=0 green=0 white=0 transmit={transmit}

[gcode_macro set_nozzle_leds_on]
gcode:
    {% set transmit=params.TRANSMIT|default(1) %}
    _set_sb_leds_by_name leds="nozzle" color="on" transmit={transmit}

[gcode_macro set_nozzle_leds_off]
gcode:
    {% set transmit=params.TRANSMIT|default(1) %}
    _set_sb_leds_by_name leds="nozzle" color="off" transmit={transmit}
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

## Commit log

2025-01-20 Tap Adapter with X Offset Adapter
    [T500 TAP Adapter.stl]
2025-02-01 Rename SB_Bambu_ Back.stl to OptionalSTLS/SB_Bambu_ Back.stl
    [SB_Bambu_ Back.stl]
